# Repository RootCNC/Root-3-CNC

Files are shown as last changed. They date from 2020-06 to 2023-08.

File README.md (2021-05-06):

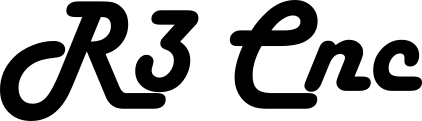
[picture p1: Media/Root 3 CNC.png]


# Root 3 CNC - 3D Printed CNC Machine 

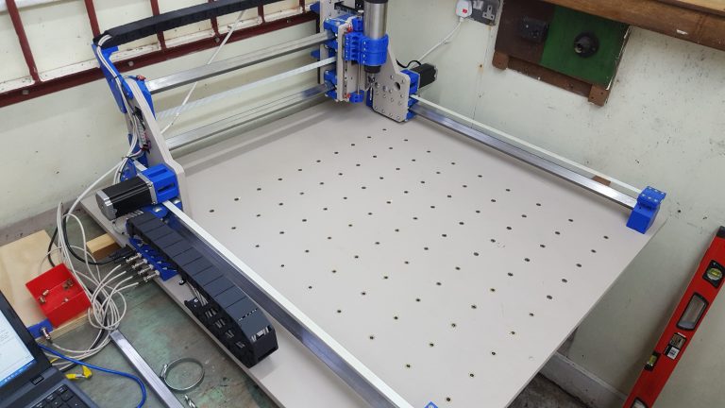
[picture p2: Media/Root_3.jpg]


R3 is the third incarnation of the Root CNC. I have been completely blown away with the community which has been created by this project and listening to all the comments and suggestions made – R3 was created. R3 Is keeping to the same design goals as before, but since then a lot has been learnt and areas for improvements been highlighted. There have been many changes implemented on this revision, some radical and some minor though all the changes have been implemented to increase configurability, rigidity, flexibility, accuracy and also reduce the amount of different parts required.

R3 now supports the largest of NEMA23 motors and also the NEMA17s motors depending on the user’s configuration. Its accuracy has also been increased by the removal of the second loop of belt on the Y-Axis whilst still keeping the two side of the gantry still connected together. The second loop of belt introduced a position error when a load was applied to the gantry, now there is only single belt length to increase its positional accuracy. By doing this made it difficult to keep the two sides of the gantry relatives to one another (something another 3D printed CNCs suffer with). Though R3 gantry sides are connected together, so no matter if the machine losses power or is disconnect the machine still stays relevant to one another to keep its running true and square.

Belt or Lead screw? This has been an interesting topic but no matter what your preference is, R3 has provisions for a Lead screws as drive mechanism for both the X and Y Axis. This does require some of your own design work to fit the type of Lead screw the individual is running though the core R3 shouldn’t need any modification and will work with Belt of Lead screws.

Linear guides for the Z axis?! I know theses aren’t considered cheap. But once all the variables and benefits have been factored in, they become a compelling option to use. especially for the short lengths the Z axis requires. With the original design (R2) there was sufficient play in the carriage, due to its minimalist design. Though R3 has attempted to removed or possibility of play with the wood panel and the use of Linear guides. But don’t think this is the only limited to linear guides, R3 keeps legacy support implementing the same linear bearing style design and also legacy Z carriages.
## Goals

 - Create an expandable CNC machine capable to machine aluminium
 - Use minimal different 3D printed parts 
 - Customization (Make it Bigger)
 - Use different motor and drive methods
 - Cheap   
 - Simple  
 - Use parts commonly used in DIY 3D printer   
 - Easily sourced parts
## BOM (Bill Of Materials)
see [HERE for more information](https://rootcnc.com/machines/root-3/bill-of-materials/)
## Where can I download it from
For the latest and greatest - please use GitHub
Github (Latest files) - [LINK](https://github.com/RootCNC/Root-3-CNC) 
Thingiverse - [LINK](https://www.thingiverse.com/thing:1750276)
## Videos
### Assembly guilds 
(http://www.youtube.com/watch?v=VfKX0M21cGE "")
### Milling Plywood
(http://www.youtube.com/watch?v=CBPlBkgISfY "")
### First Movements
(http://www.youtube.com/watch?v=zV66W9bVTgU "")
### Dry Run
(http://www.youtube.com/watch?v=VkSvLdQc4Qw "")

## License

This project is licensed under the Creative Commons 4.0 license with 
Attribution-NonCommerial-ShareAlike see `LICENSE.txt` for details

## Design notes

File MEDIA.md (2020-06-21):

# Media
Links to non-official videos of the Root 3 cnc. Just a few of the videos that the community has created. Feel free to add more!

## Demonstrations
- [plasma cutter](https://www.youtube.com/watch?v=4bUiL51nPEU)
- [mdf](https://www.youtube.com/watch?v=HNyUsCajYws)
- [laser, in polish](https://www.youtube.com/watch?v=8oZk74TXRVo)
- [laser](https://www.youtube.com/watch?v=Lp46dZl_eGw)
- [mdf, from sailorpete himself](https://www.youtube.com/watch?v=v6d2QQCTKL8)
- [plywood](https://www.youtube.com/watch?v=qoaiHhIS8y8)
- [no cutting, just moving](https://www.youtube.com/watch?v=_PqRj57KkUw)
- [dremel 3000 as spindle](https://www.youtube.com/watch?v=9FLgetXrfY0)
- [plywood, with dust shoe)(https://www.youtube.com/watch?v=5yzxbGJIvBg)

## Build process
- [Timelapse of first half of build, no voiceover](https://www.youtube.com/watch?v=sJdK4KLR89o)
- [second half of build, no voiceover](https://www.youtube.com/watch?v=9sj80fLrxw4)
- [carriages assembly, has a great google doc in the description](https://www.youtube.com/watch?v=mLDNwsXnJGA)
- [box section carriages assembly, has a great google doc in the description)(https://www.youtube.com/watch?v=ErkqIhtdq1w)

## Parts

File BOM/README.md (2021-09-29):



# Root 3 CNC Bill of materials
The Root 3 CNC is configurable in many ways, here are a few configurations you'll need to consider before building one.

Please note an Excel document can be downloaded for more information - [Link](https://github.com/RootCNC/Root-3-CNC/blob/master/BOM/R3%20BOM.xlsx)
#### Belt Options:
 - 2mm GT2 Belts
 - 3mm HTD Belts (Advised option)
#### Box section Options
 - 25x25mm Box section (Metric) 
 - 1"x1" Box section (Imperial)
#### Motor Section
Root 3 CNC can accommodate either NEMA 17 or NEMA 23 Motors. If budget allows, I would recommend the NEMA 23 motor defined in the list below
### Spindle Options
Root 3 supports a number of Spindle sizes:
 - 52mm
 - 65mm
 - 80mm
#### Coach bolts
Coach bolts are optional for the 3D printed carriage if you want a low profile mounting. if you choose to use coach bolts to mount the two carriages together, then you'll need half coach and half standard (this information in the Excel Bill of Materials)
# 3D Printed Parts required
Please note the Root 3 CNC machine can be configured for **different belt sizes** and **different box section sizes**. 
| 3D Printed Parts | Required | QTY | Alternative |
|---|---|---|---|
| Box Section Linear (\*1) | YES | 8 ||
| Y Axis Bar Mount (\*2) (\*3) Mirror | YES | 2 ||
| Y Axis Bar Mount (\*2) (\*3) STD | YES | 2 ||
| X Axis Belt Clamp (\*3) Belt Plate | YES | 2 ||
| X Axis Belt Clamp (\*3) | YES | 2 ||
| Motor Mount (\*4)| YES | 2 ||
| 50mm Spacer (\*4)| YES | 2 ||
| X Carriage Belt Idler | YES | 1 ||
| Y Axis Dust Cover Spacer | NO | 4 ||
| Y Gantry Bearing Cap | YES | 1 |
| Y Gantry Bearing Cap (Cable mount) | YES | 1 ||
| Y Gantry Bearing Space | YES | 2 ||
| Y Gantry Box Mount Foot | YES | 4 |
| Y Gantry Box Section Belt Clamp | YES | 4 ||
| Y Gantry Motion Link | YES | 2 ||
| Z Axis Bearing Cup Bottom | YES | 1 ||
| Z Axis Bearing Cup Top | YES | 1 |Z Axis Bearing Cup Top - Limit Tab Removed<br />Allows clearance for router (Makita in my case) by removing the upper Z limit switch tab |
| MGN 12 Spindle mount (\*5) (Text) | YES | 1 ||
| MGN 12 Spindle mount (\*5)  | YES | 1 ||
| X Axis Drag Chain mount X carriage | YES | 1 ||
| X Axis Drag Chain Mount Y Side panel | YES | 1 ||
| Y Axis Drag Chain mount to  X carriage | YES | 1 ||
| Drag Chain Y Carriage Mount | YES | 1 ||

(\*1) Optional Configuration: for standard M8 Bolts print x8 Guild STD and for Coach bolt print x8 Guild STD and 4x COACH BOLT
(\*2) Select box section size
(\*3) Select Belt type 
(\*4) Select Motr size 
(\*5) Select Spindle size 

# Panels
| Item | QTY | Link|
|---|---|-----|
| Side_Panel|2|[Root CNC Store](https://rootcnc.com/product/root-3-side-panel/)|
| Z_Axis_WoodPanel_Front|1|[Root CNC Store](https://rootcnc.com/product/root-3-front-rear-x-carriage-z-plate/)|
| Z_Axis_WoodPanel_Rear|1|[Root CNC Store](https://rootcnc.com/product/root-3-front-rear-x-carriage-z-plate/)|

Wooden Panel kits can be found [HERE](https://rootcnc.com/product/root-3-cnc-starter-pack/) 

# Electronics/ Electro Mechanical
| Item | Required | QTY | Link|
|---|---|---|-----|
| 23HS41-1804S NEMA 23 1.8deg 2.4Nm (340oz.in) 1.8A | YES | 4 | [LINK](https://www.omc-stepperonline.com/nema-23-bipolar-1-8deg-2-4nm-340oz-in-1-8a-4-95v-57x57x104mm-4-wires.html/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)|
| NEMA 17 Bipolar 1.8deg 65Ncm (92oz.in) 2.1A |NO |4| [LINK](https://www.omc-stepperonline.com/nema-17-bipolar-1-8deg-65ncm-92oz-in-2-1a-3-36v-42x42x60mm-4-wires-it.html/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)|
| 1.5KW Spindle with VFD|YES|1|[LINK_1](https://s.click.aliexpress.com/e/_dX0JKm3) [LINK_2](https://s.click.aliexpress.com/e/_dT4xs63) [LINK_3](https://s.click.aliexpress.com/e/_dSjt6gr) [LINK_4](https://s.click.aliexpress.com/e/_dSUhh43)
| 400W Quiet Spindle (not recommended)|NO |||
| Micro Switch SPDT micro switch V4 KW11i|YES|6|[LINK UK](https://amzn.to/31Kf1wC) [LINK](https://s.click.aliexpress.com/e/_ATnQCz)| 
| 12V or 24V PSU (For Controller power + any lights) |YES|1|[12V_LINK_UK](https://amzn.to/2HxYvIS) [12V_lINK](https://s.click.aliexpress.com/e/_AACYyd)| 
| Aviation plug (GX12) |NO|x|[LINK_UK](https://amzn.to/31LBPfl) [LINK](https://s.click.aliexpress.com/e/_AtqbWz)|
| Stepper Motor Drivers (E.G DRV8825)| YES | 4||
| Cooling Fan - 60mm DC Fan | YES | 1 ||
| 4 Core AWG24/26 Cable | YES |||
| Arduino Mega With RAMP kit ||||
| Root CNC GRBL controller comming soon ||||

# Motion
| Item | Required | QTY | Link|
|---|---|---|-----|
|608 Bearings | Yes | 56 |[LINK_UK](https://amzn.to/3dWB9c6) [LINK](https://s.click.aliexpress.com/e/_ATuujF)|
|MGN12 200mm + (MGN12C x2) | Yes | 2 |[LINK]()|
|R38 18mm x 37mm Black Drag Chain 1M | Yes | CNC Size dependant |[LINK_UK](https://amzn.to/37J6PAH)  [LINK](https://s.click.aliexpress.com/e/_9hJS33)|
|3M HTD Belt | Yes | CNC Size dependant (2x Y Axis Length + 1x X Axis Length = min belt length) |[LINK_UK]()  [LINK]()|
|HTD 3M Round Tooth Timing Belt Pulley 8mm Bore 24T*| Yes | 5/7 |[LINK]()|
|HTD 3M Round Tooth Timing Belt Pulley 8mm Bor 20T*| Yes | 2 |[LINK]() |
|HTD 3M Round Tooth Timing Belt 9mm Wide 345-3M-9| Yes | 1 |[LINK_UK]() [LINK]()

(\*) Dependant on stepper motor selection - This configuration will work for the above stepper motor from OMC Stepper Motor Online

# Hardware
Below is guide on the QTY required/ the pack sizes I brought to assemble the Root 3 CNC
| Item | Required | QTY | Link|
|---|---|---|-----|
|Box section 25x25xX/Yx3mm (W,D,L,T)(\*)|YES|4||
|M3 Penny Washers (Large)|YES|100|YES||
|M3 Machine Screws (16,20,25,30,40 mm)|YES|100|YES||
|M3 Nuts|YES|100|YES||
|M3 Rivit Nuts|YES|16|YES||
|M4 Penny Washers (Large)|YES|30|YES||
|M4 x40mm Bolt|YES|20|YES||
|M4 x 35mm Countersunk Screw|YES|32|YES||
|M4 Nuts|YES|50|YES||
|M5 x70mm Bolt with Washer head|YES|8|YES||
|M5 Washers|YES|8|YES||
|M5 Nuts|YES|8|YES||
|M8 Axis Connecting Bar|YES|1|YES||
|M8 Lead screw / Threaded Rod|YES|1|YES||
|M8 x25mm Herx Head Bolt|YES|32|YES||
|M8 x75mm Bolt|YES|20|YES||
|M8 x75mm Coach Bolt|NO|20|NO||
|M8 Washers|YES|100|YES||
|M8 Nuts|YES|100|YES||
|M8 Collar|YES|4|YES||
|M8 Tee Nuts|NO||NO||

(\*) Length of the box section is dependant on size of the machine you are building - use this link for more information [LINK](https://rootcnc.com/machines/root-3/root-3-dimensions/)

# MISC Items
| Item | Required | QTY | Link|
|---|---|---|-----|
|Mist Coolant Lubrication Spray System Unit (Used for Airline to Spindle - Aluminium machining)| No |1 | |

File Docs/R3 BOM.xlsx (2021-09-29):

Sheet: 3D Printed Parts
Item | QTY | Printed | Config | Stepper Config | 1" or 25mm Box | Belt Size | Notes
Box Section Linear Guild STD | 8 | No | Default | N/A | N/A | N/A
* Optional Config |  |  |  |  |  |  | Results in a tidyer looking machine but does require M8 Coach bolts with filled edges
-- Box Section Linear Guild STD | 4 | No | Optional | N/A | N/A | N/A
-- Box Section Linear Guild COACH BOLT | 4 | No | Optional | N/A | N/A | N/A
1" Square Box section |  |  |  |  |  |  | Use this subsection over 25mm box section if you plan to use 1" box section
-- X Axis Box Section Mount 1'x1' | 2 | No | Default | N/A | 1" | N/A
* 2mm Pitch belt
-- Y Axis Bar Mount 1'x1' 2mm Mirror | 2 | No | Default | N/A | 1" | GT2 (2mm)
-- Y Axis Bar Mount 1'x1' 2mm STD | 2 | No | Default | N/A | 1" | GT2 (2mm)
-- X Axis Belt Clamp 2mm GT2 Belt Plate | 2 | No | Default | N/A | 1" | GT2 (2mm)
-- X Axis Belt Clamp 2mm GT2 | 2 | No | Default | N/A | 1" | GT2 (2mm)
* 3mm Pitch Belt
-- Y Axis Bar Mount 1'x1' 3mm Mirror | 2 | No | Default | N/A | 1" | 3M HTD (3mm)
-- Y Axis Bar Mount 1'x1' 3mm STD | 2 | No | Default | N/A | 1" | 3M HTD (3mm)
-- X Axis Belt Clamp 2mm 3M HTD Belt Plate | 2 | No | Default | N/A | 1" | 3M HTD (3mm)
-- X Axis Belt Clamp 2mm 3M HTD | 2 | No | Default | N/A | 1" | 3M HTD (3mm)
25mm Square Box section |  |  |  |  |  |  | Use this subsection over 1" box section if you plan to use 25mm box section
-- X Axis Box Section Mount 25x25 | 2 | No | Default | N/A | 25mm | N/A
* 2mm Pitch belt
-- Y Axis Bar Mount 25x25 2mm Mirror | 2 | No | Default | N/A | 25mm | GT2 (2mm)
-- Y Axis Bar Mount 25x25 2mm STD | 2 | No | Default | N/A | 25mm | GT2 (2mm)
-- X Axis Belt Clamp 2mm GT2 Belt Plate | 2 | No | Default | N/A | 25mm | GT2 (2mm)
-- X Axis Belt Clamp 2mm GT2 | 2 | No | Default | N/A | 25mm | GT2 (2mm)
* 3mm Pitch Belt
-- Y Axis Bar Mount 25x25 3mm Mirror | 2 | No | Default | N/A | 25mm | 3M HTD (3mm)
-- Y Axis Bar Mount 25x25 3mm STD | 2 | No | Default | N/A | 25mm | 3M HTD (3mm)
-- X Axis Belt Clamp 2mm 3M HTD Belt Plate | 2 | No | Default | N/A | 25mm | 3M HTD (3mm)
-- X Axis Belt Clamp 2mm 3M HTD | 2 | No | Default | N/A | 25mm | 3M HTD (3mm)
Motor Mount NEMA17 | 2 | No | Optional | NEMA17 | N/A | N/A
NEMA17 50mm Spacer | 2 | No | Optional | NEMA17 | N/A | N/A
Motor Mount NEMA23 | 2 | No | Default | NEMA23 | N/A | N/A
NEMA23 50mm Spacer | 2 | No | Default | NEMA23 | N/A | N/A
X Carriage Belt Idler | 1 | No | Default | N/A | N/A | N/A
Y Axis Dust Cover Spacer | 4 | No | Optional | N/A | N/A | N/A | Spacer when fitting dust cover to the Y axis
Y Gantry Bearing Cap | 1 | No | Default | N/A | N/A | N/A
Y Gantry Bearing Cap (Cable mount) | 1 | No | Default | N/A | N/A | N/A
* Optional Config |  |  |  |  |  |  | If cable management is required
-- Y Gantry Bearing Cap | 1 | No | Optional | N/A | N/A | N/A
-- Y Gantry Bearing Cap W/ cable clip | 1 | No | Optional | N/A | N/A | N/A
Y Gantry Bearing Space | 2 | No | Default | N/A | N/A | N/A
Y Gantry Box Mount Foot | 4 | No | Default | N/A | N/A | N/A
Y Gantry Box Section Belt Clamp | 4 | No | Default | N/A | N/A | N/A
Y Gantry Motion Link | 2 | No | Default | N/A | N/A | N/A
Z Carriage - Linear Guild (Recomened)
Z Axis Bearing Cup Bottom | 1 | No | Default | N/A | N/A | N/A
Z Axis Bearing Cup Top | 1 | No | Default | N/A | N/A | N/A
Z Axis Bearing Cup Top - Limit Tab Removed | 1 | No | Optional | N/A | N/A | N/A | Allows clearance for router (Makita in my case) by removing the upper Z limit switch tab
Spindle Options
MGN 12 Spindle mount 52mm (Text) | 1 | No | Optional | N/A | N/A | N/A
MGN 12 Spindle mount 52mm (NO Text) | 1 | No | Optional | N/A | N/A | N/A
MGN 12 Spindle mount 65mm (Text) | 1 | No | Default | N/A | N/A | N/A | I currently us a VFD spindle
MGN 12 Spindle mount 65mm (NO Text) | 1 | No | Default | N/A | N/A | N/A | I currently us a VFD spindle
MGN 12 Spindle mount 80mm (Text) | 1 | No | Optional | N/A | N/A | N/A
MGN 12 Spindle mount 80mm (NO Text) | 1 | No | Optional | N/A | N/A | N/A
X Axis Drag Chain mount X carriage | 1 | No | Default | N/A | N/A | N/A
X Axis Drag Chain Mount Y Side panel | 1 | No | Default | N/A | N/A | N/A
Y Axis Drag Chain mount to X carriage | 1 | No | Default | N/A | N/A | N/A
Drag Chain Y Carriage Mount | 1 | No | Default | N/A | N/A | N/A

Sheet: Nut and Bolt
Item | QTY | Config | Stepper Config | 1" or 25mm Box | Belt Size | Notes
M3 Penny Washers (Large) | Lots
M3 Machine Screws (Different lengths) | Lots |  |  |  |  | x16,20,25,30,40 mm Lengths (good to have a selection on hand)
M3 Nuts | Lots
M3 Rivit Nuts | 16 |  |  |  |  | (FN02991) used to mount the MGN rail to the wooden board
M4 Penny Washers (Large) | Lots | Default | N/A | N/A | N/A
M4 x40mm Bolt | 20
M4 x 35mm Countersunk Screw | 32
M4 Nuts | Lots
M5 x70mm Bolt with Washer head | 8 |  | NEMA23 |  |  | Used on the Y axis side pannel to mount the Nema 23s
M5 Washers | 8
M5 Nuts | 8 |  |  |  |  | Used on the Y axis side pannel to mount the Nema 23s
M8 Axis Connecting Bar | 1 |  |  |  |  | Length is size dependant on machine
M8 Lead screw / Threaded Rod | 1 |  |  |  |  | 400mm cut to length
M8 x25mm Herx Head Bolt | 32
M8 x75mm Bolt | 20 | Default
M8 x75mm Coach Bolt | 20 | Optional
M8 Washers | Lots
M8 Nuts | Lots
M8 Collar | 4
M8 Tee Nuts |  | Optional |  |  |  | Used to mount work pieces to the bed
MGN12 200mm | 2
MGN12C | 4
3M HTD Belt | 1 |  |  |  |  | Length is size dependant on machine
24T 3M HTD 8mm Pulley | 5/7 |  |  |  |  | Used on the X/Y Axis Motion note the bore of your stepper motors!
20T 3M HTD 8mm Pulley | 2 |  |  |  |  | Used for the Z Axis
345-3M-9 | 1 |  | NEMA23 |  |  | Used to link the Z axis
608 Bearing | 56
Drag Chain 18x37mm Open | 2
Aluminum Box section 25x25xX/Yx3mm (W,D,L,T) | 4 | Default | N/A
Steel Box section 25x25xX/Yx2mm (W,D,L,T) | 4 | Optional | N/A

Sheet: Electronics
Item | QTY | Ordered? | Notes
PSU | 1 | No
-12V 100W+ (Stepper motors Only) |  | No | Currently use a over kill 400W PSU for Stepper motors only
- Spindle PSU (Dependant on Spindle choose!) |  | No | Will be required with DC motors Like the orginal used in R2
Stepper Motor Drivers | 4 | No
- DRV8825 |  | No | Currently used on R2 & R2.1
- A4988 |  | No | I would recomd the DRV8825 driver instead of theses
- More to come… |  | No
Stepper Motors | 4 | No
- NEMA 17 |  | No
--- 42BYGHW609 4000g/cm 1.7A |  | No | Used on R2 Y,Z axis
--- 17HS24-2104S |  | No | Used on R2 X axis
- NEMA 23 |  | No
---23HS41-1804S |  | No | Currently used on all axis on R2.1
Motion Controller | 1 | No
- Arduino Mega (Ramps 1.4 - Marlin Firmware) |  | No | Currently used on all my machines
- Arduino Uno (GRBL with CNC sheild) |  | No | Not used
Endstops | 6 | No
- KW11 Micro switches |  | No | Used on all my machines
- LJ12A3-4-Z/BY Inductive Sensor |  | No | My ideal option but more costly
Controller/ Stepper motor driver Cooling Fan | 1 | No
- 60mm DC Fan |  | No | Or other Size but needed to keep the drivers running cool
Cabling |  | No
- 4 Core AWG24/26 Cable |  | No | Used for Stepper motors and Endstop
~~- Ethernet Cable~~ |  | No | Not recommened due to high chance of breakage due to movement (Google "Work Hardening" - due to the single cores/strand used it Cat cabling)
Spindle | 1 | No
- Quiet Cut Spindle (300W 48V DC motor) |  | No | Used on R2 Requires an aditional PSU as stated un PSU section
- 400W 48V DC motor |  | No | Requires an aditional PSU as stated un PSU section
- VDF Spindle |  | No | Currently using a 1.5kW aircooled VFD spindle on R2.1 well worht it ( 1.5KW Air-cooled Spindle motor/ .5kw Variable Frequency Drive inverter)

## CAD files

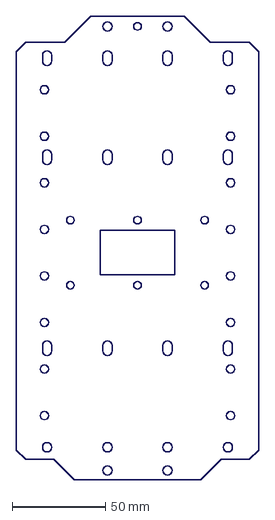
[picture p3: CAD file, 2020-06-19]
DXF_Files/X Carriage Rework wood pannel FRONT.DXF
130.0 x 249.0 mm

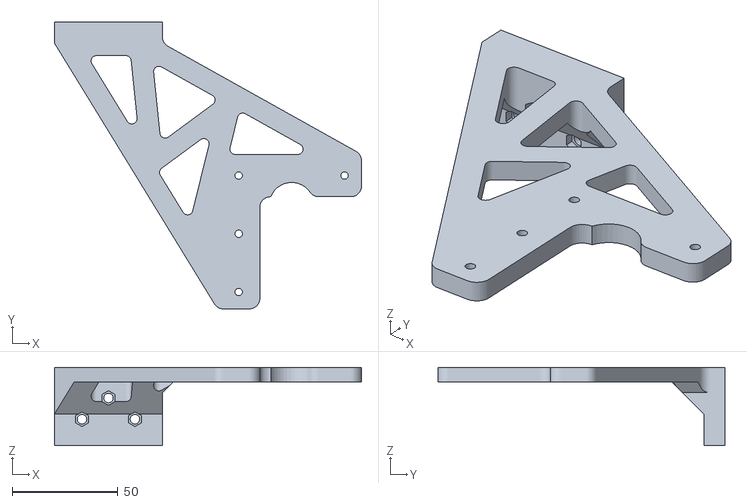
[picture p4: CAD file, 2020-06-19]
STL_Files/Drag Chain Mounts/X Axis/X Axis Drag Chain Mount Y Side panel.STL
145.0 x 135.5 x 37.0

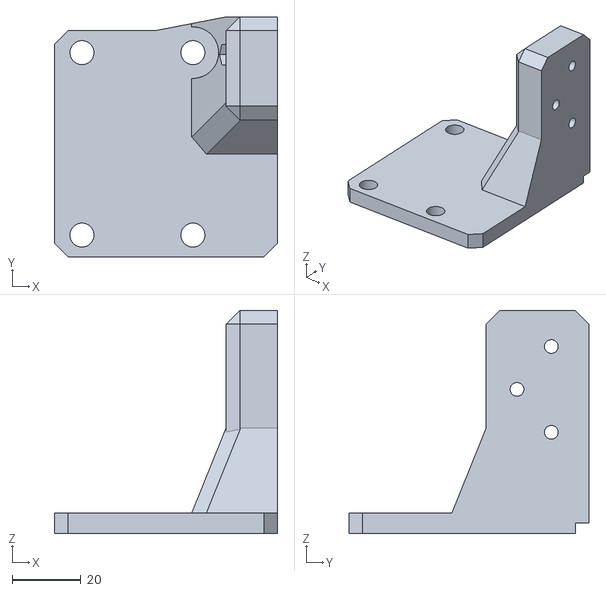
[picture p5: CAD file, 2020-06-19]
STL_Files/Drag Chain Mounts/Y-Axis/Drag Chain Y Carriage Mount.STL
65.0 x 70.0 x 65.0

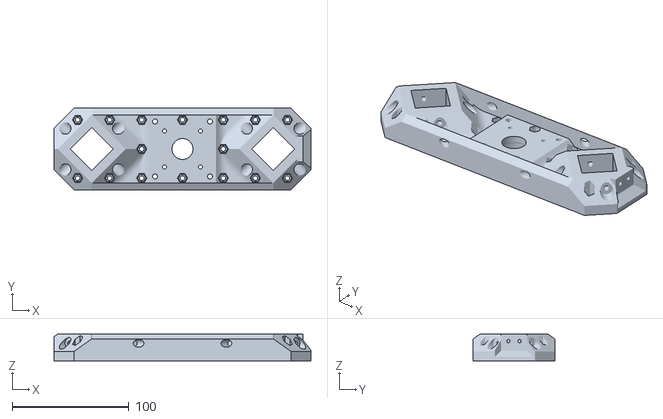
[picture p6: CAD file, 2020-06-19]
STL_Files/X Carriage/1'x1'/X Axis Box Section Mount 1'x1'.STL
220.6 x 70.0 x 23.0

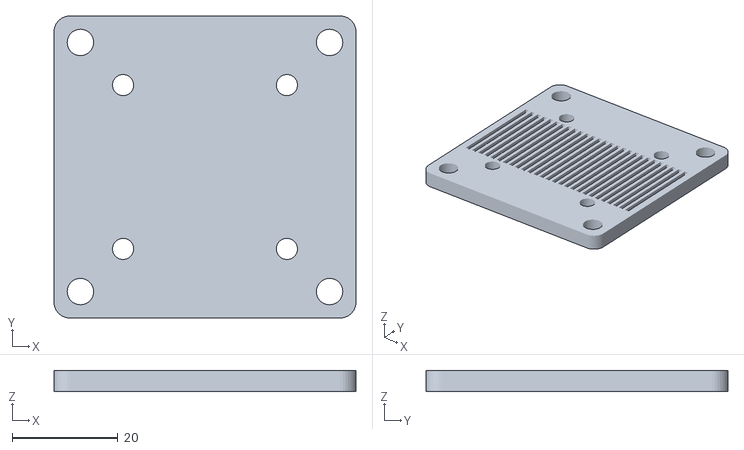
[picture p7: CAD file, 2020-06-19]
STL_Files/X Carriage/X Axis Belt Clamp 2mm GT2 Belt Plate.STL
57.1 x 57.1 x 4.00

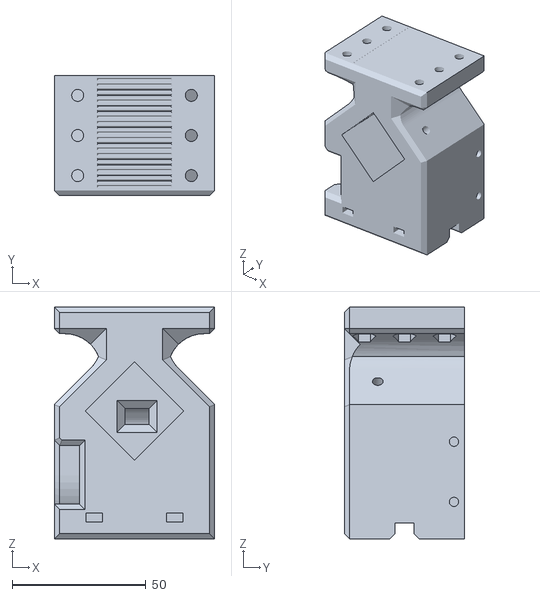
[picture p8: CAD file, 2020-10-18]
STL_Files/Y Carrage/1'x1'/2mm Pitch Belt/Y Axis Bar Mount 1'x1' 2mm STD IssB.STL
60.0 x 45.0 x 86.8

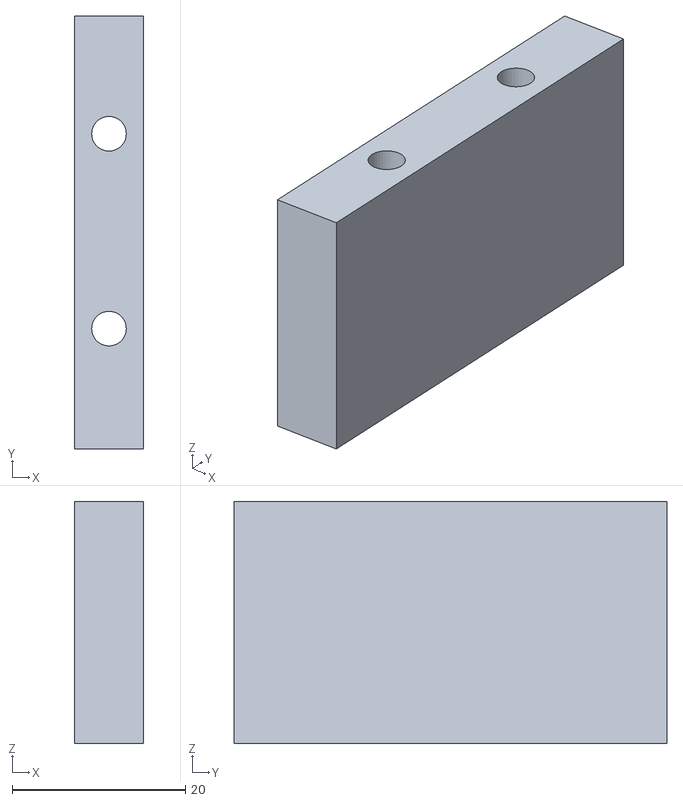
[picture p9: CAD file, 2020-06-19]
STL_Files/Y Carrage/Y Axis Dust Cover Spacer.STL
8.00 x 50.0 x 28.0

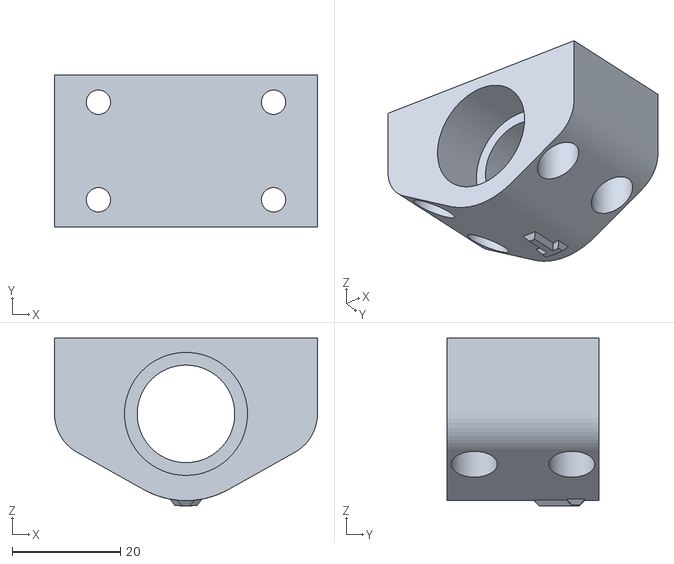
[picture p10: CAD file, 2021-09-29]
STL_Files/Z Axis/Linear Guild (Recomenned)/Z Axis Bearing Cup Top - Limit Tab Removed.stl
48.5 x 28.0 x 31.0

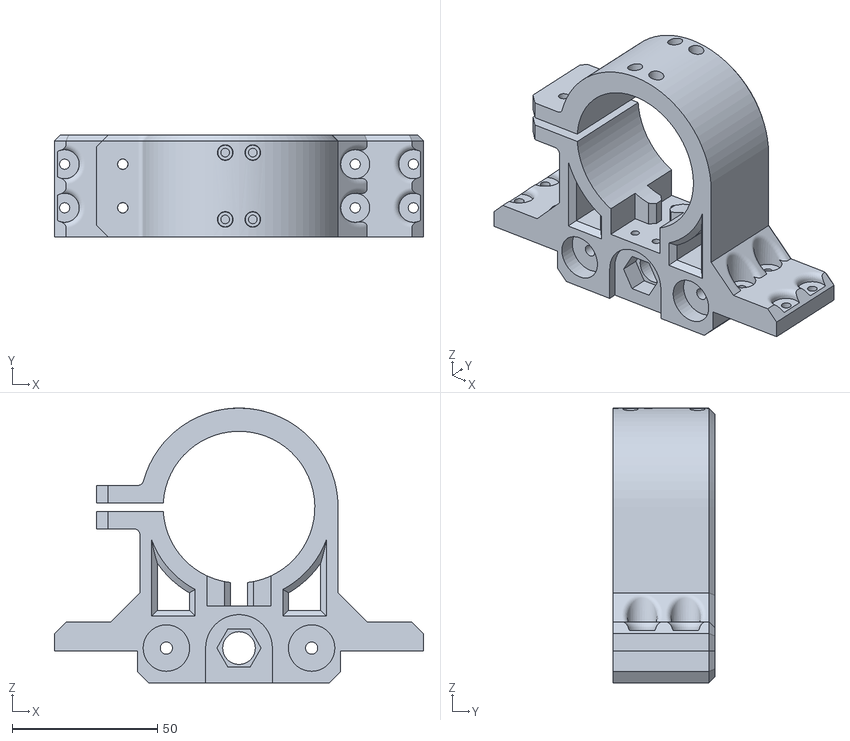
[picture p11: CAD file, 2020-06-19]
STL_Files/Z Axis/Linear Guild (Recomenned)/Z Carriages/52mm/MGN 12 Spindle mount 52mm (NO Text).STL
127.0 x 35.0 x 94.6

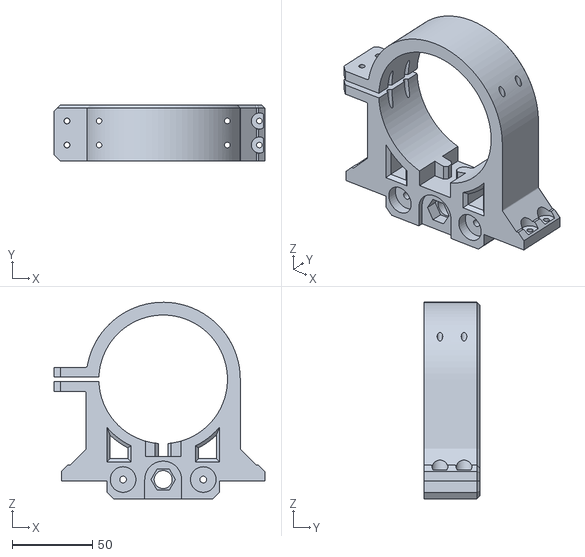
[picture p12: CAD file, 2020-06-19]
STL_Files/Z Axis/Linear Guild (Recomenned)/Z Carriages/80mm/MGN 12 Spindle mount 80mm (NO Text).STL
131.6 x 35.0 x 122.6

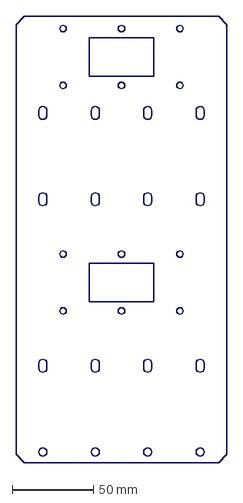
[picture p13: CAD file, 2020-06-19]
DXF_Files/X Carriage Rework wood pannel BACK.DXF
130.0 x 275.0 mm

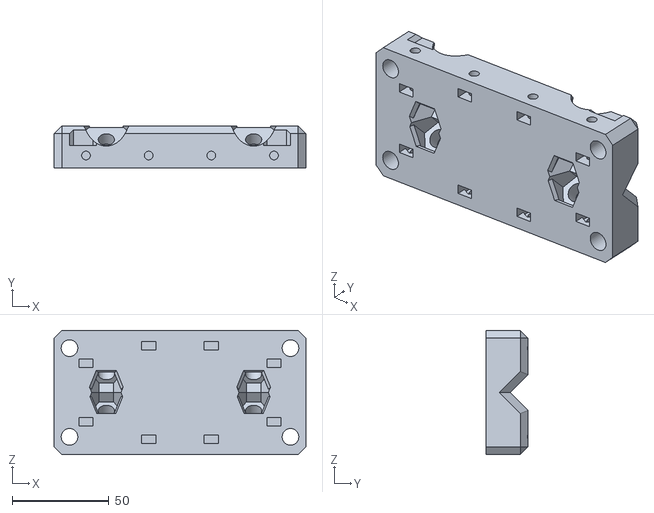
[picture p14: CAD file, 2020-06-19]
STL_Files/Box Section Linear Guild STD.STL
130.0 x 21.8 x 64.0

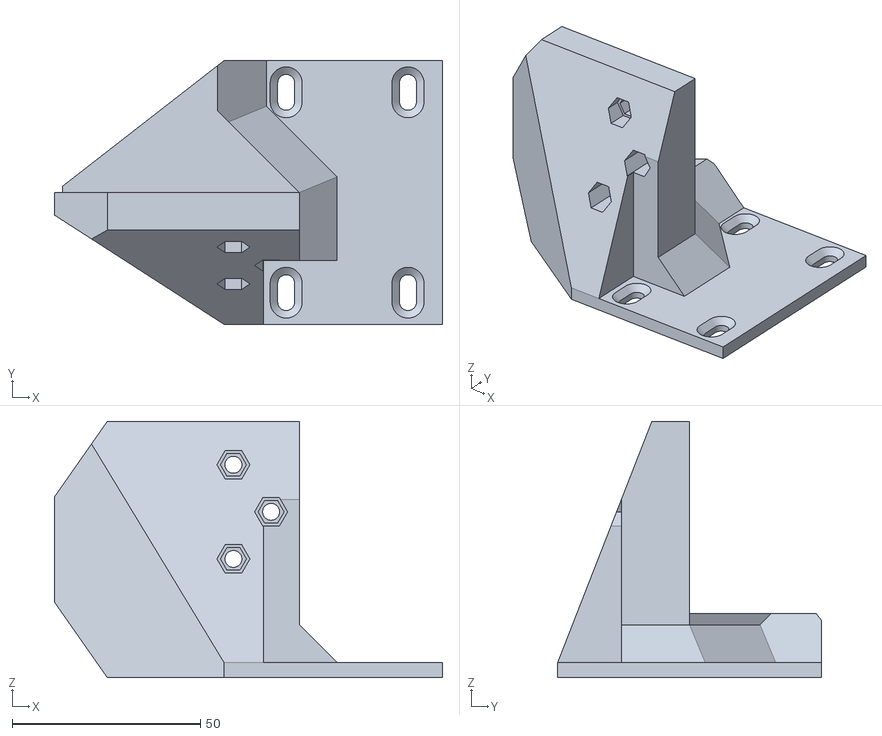
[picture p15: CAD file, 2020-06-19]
STL_Files/Drag Chain Mounts/X Axis/X Axis Drag Chain mount X carriage.STL
103.0 x 70.0 x 68.0

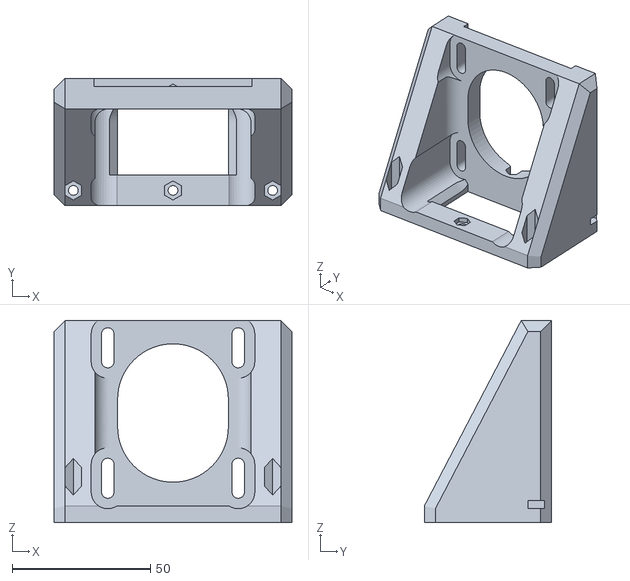
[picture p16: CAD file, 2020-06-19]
STL_Files/X Carriage/Motor Mount NEMA23.STL
86.0 x 46.0 x 73.0

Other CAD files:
STL_Files/X Carriage/25x25mm/X Axis Box Section Mount 25x25mm.STL
STL_Files/Y Carrage/1'x1'/3mm Pitch Belt/Y Axis Bar Mount 1'x1' 3mm STD IssB.STL
STL_Files/Y Carrage/25x25mm/2mm Pitch Belt/Y Axis Bar Mount 25x25 2mm STD IssB.STL
STL_Files/Y Carrage/25x25mm/3mm Pitch Belt/Y Axis Bar Mount 25x25 3mm Mirror IssB.STL
DXF_Files/X Carriage Rework wood pannel UNIVERSAL.DXF
DXF_Files/X side pannel.DXF
STL_Files/Box Section Linear Guild COACH BOLT.STL
STL_Files/Connector Panel.STL
STL_Files/Probe Mount.STL
STL_Files/X Carriage/Motor Mount NEMA17.STL
STL_Files/X Carriage/X Axis Belt Clamp 3M HTD Belt Plate.STL
STL_Files/X Carriage/X Carriage Belt Idler.STL
STL_Files/X Carriage/X axis Belt Mount 2mm.STL
STL_Files/X Carriage/X axis Belt Mount 3mm.STL
STL_Files/Y Carrage/1'x1'/2mm Pitch Belt/Y Axis Bar Mount 1'x1' 2mm Mirror IssB.STL
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

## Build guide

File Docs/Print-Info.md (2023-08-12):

---
title: Root 3 Print Orientation
description: How to print the parts for the Root 3
published: true
date: 2022-06-28T22:24:57.245Z
tags: root 3, how to print
editor: markdown
dateCreated: 2022-06-28T22:17:17.168Z
---

# Box Section Linear Guild STD
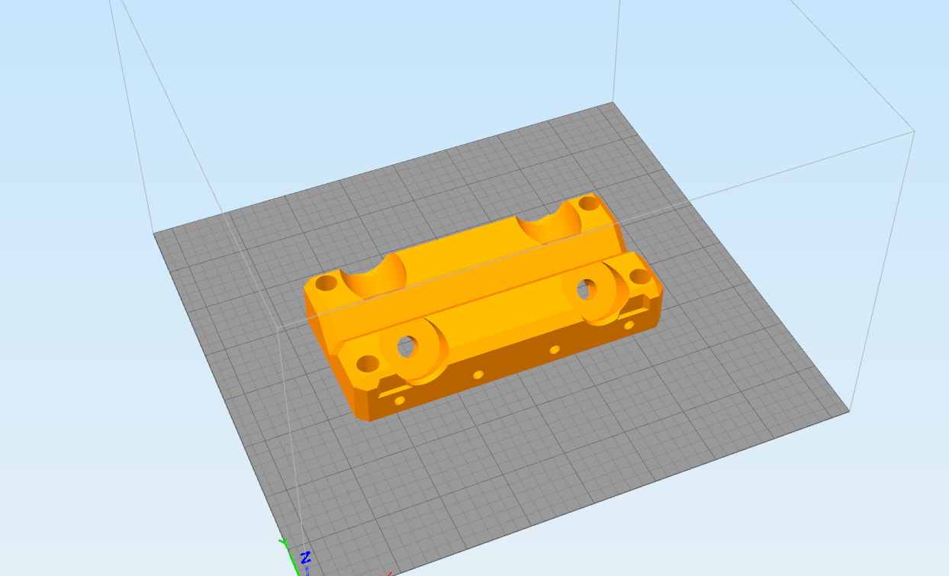
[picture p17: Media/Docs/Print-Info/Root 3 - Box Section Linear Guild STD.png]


# Connector Panel
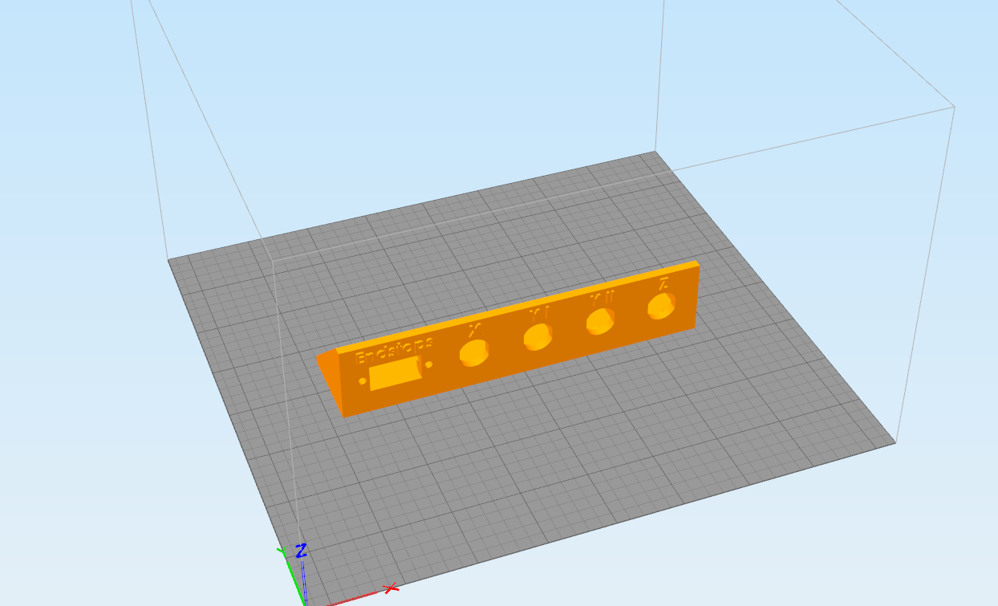
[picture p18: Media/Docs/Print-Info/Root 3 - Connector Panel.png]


# Drag Chain Y Carriage Mount
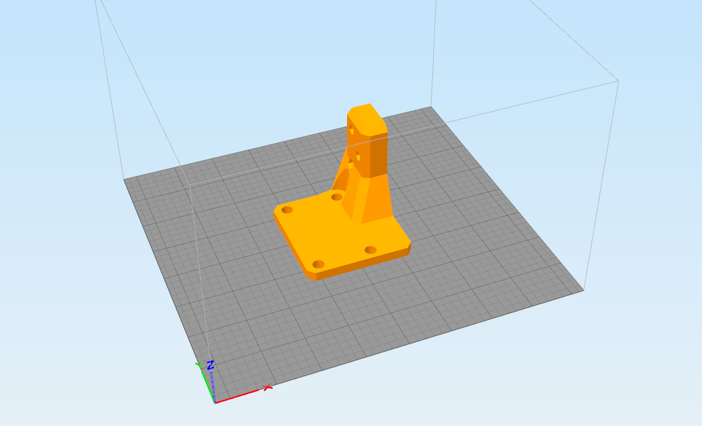
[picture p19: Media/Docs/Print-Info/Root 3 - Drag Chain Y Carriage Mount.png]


# MGN 12 Spindle mount ##mm (Text)- (NO Text)
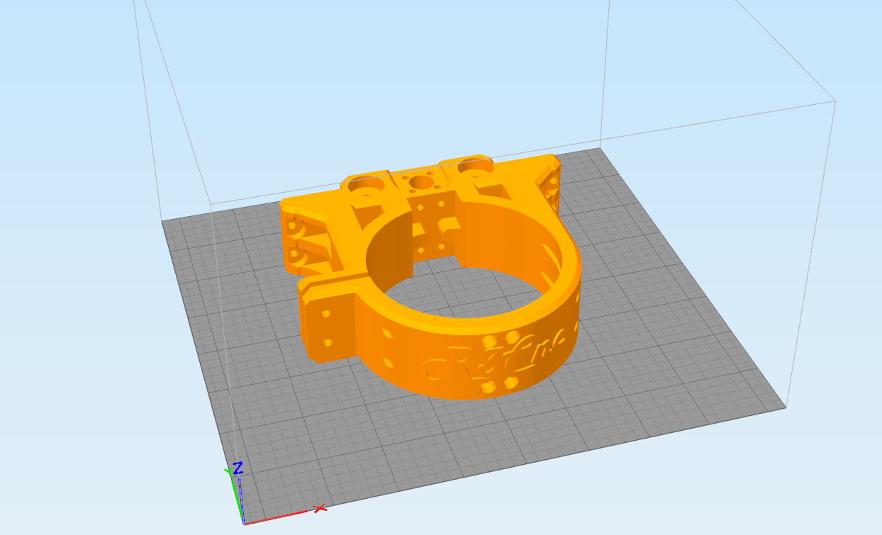
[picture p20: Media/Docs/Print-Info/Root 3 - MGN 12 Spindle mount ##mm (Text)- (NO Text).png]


# Motor Mount NEMA17
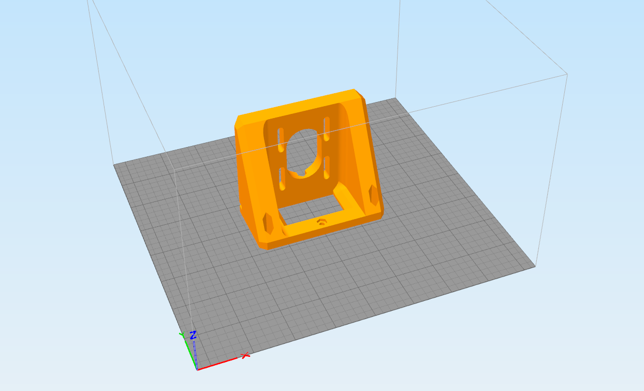
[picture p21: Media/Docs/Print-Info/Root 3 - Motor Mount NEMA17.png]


# Motor Mount NEMA23
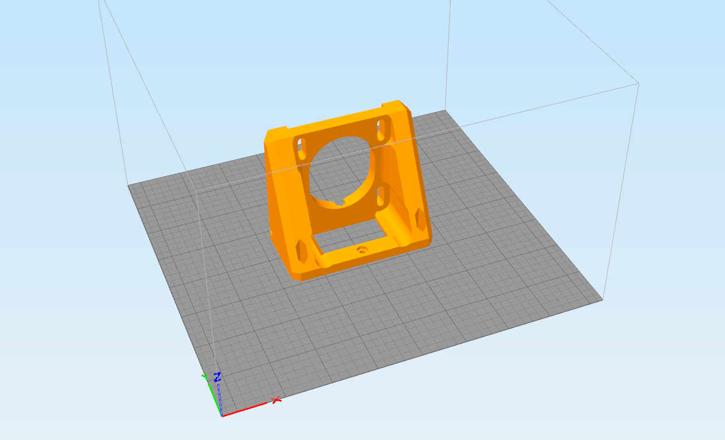
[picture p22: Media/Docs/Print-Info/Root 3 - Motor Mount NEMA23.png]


# NEMA17 50mm Spacer
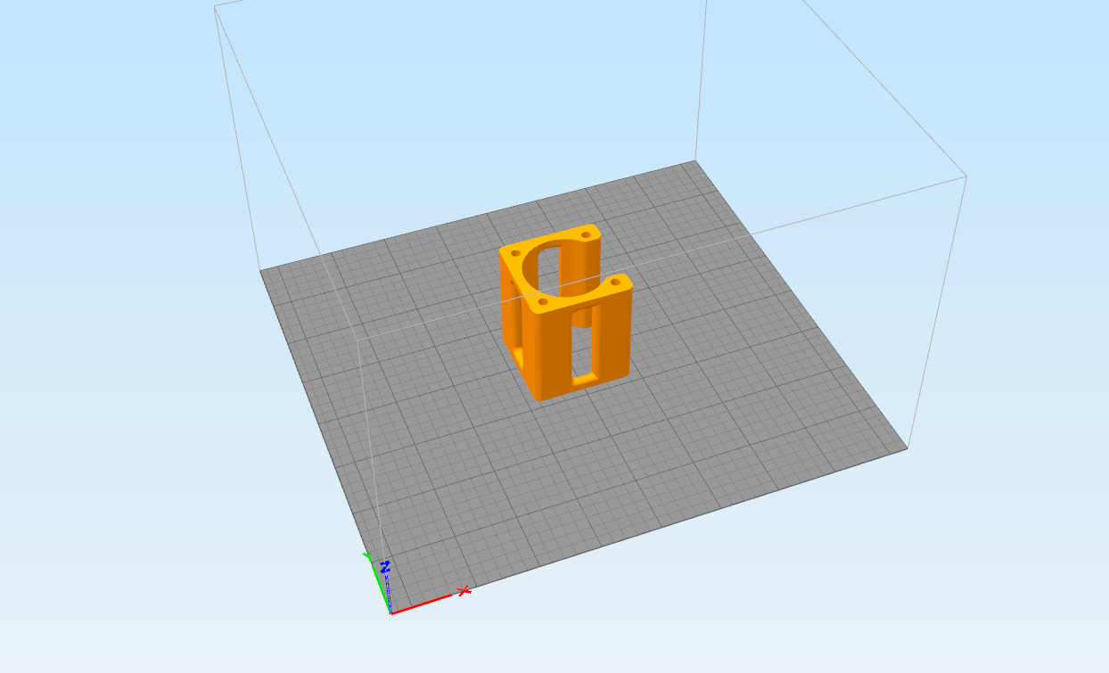
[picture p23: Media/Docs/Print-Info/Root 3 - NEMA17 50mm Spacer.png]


# NEMA23 50mm Spacer
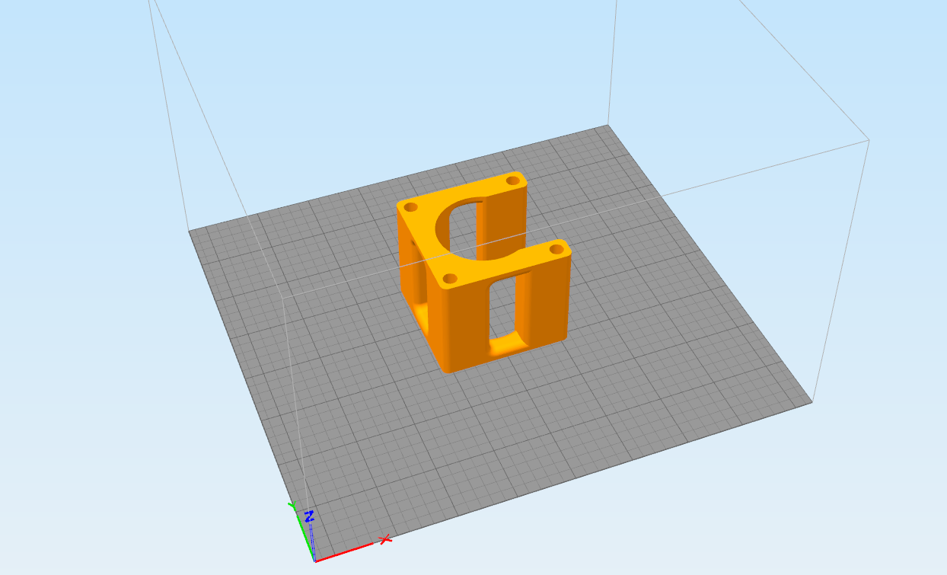
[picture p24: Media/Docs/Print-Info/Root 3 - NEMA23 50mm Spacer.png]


# X Axis Belt Clamp 2mm GT2 Belt Plate
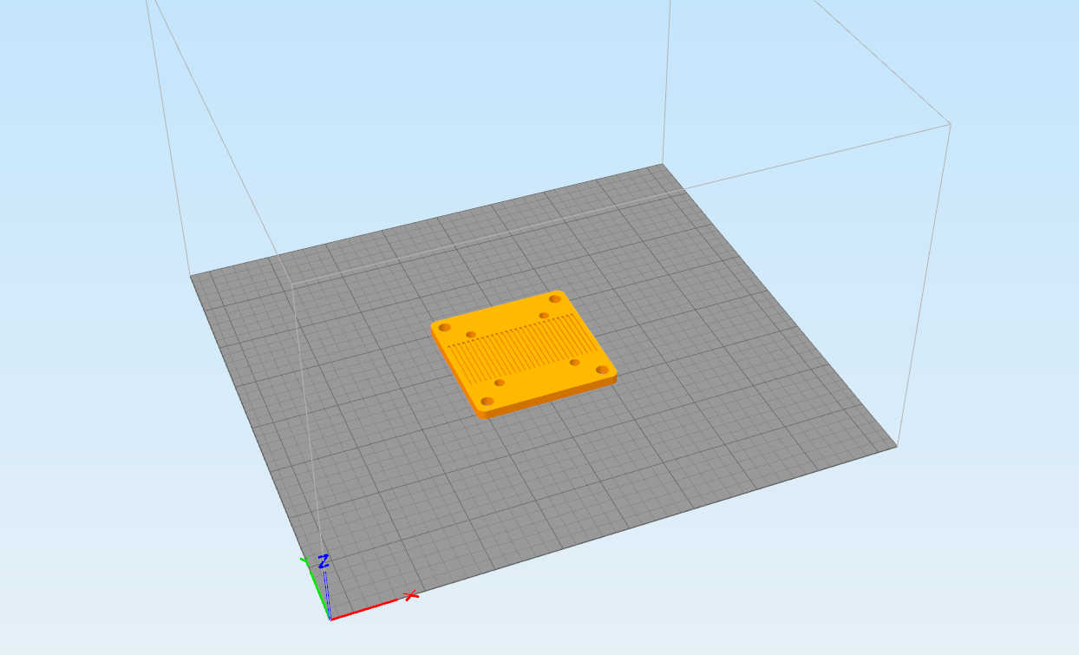
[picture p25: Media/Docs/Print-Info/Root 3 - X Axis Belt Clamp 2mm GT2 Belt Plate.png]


# X Axis Belt Clamp 3M HTD Belt Plate
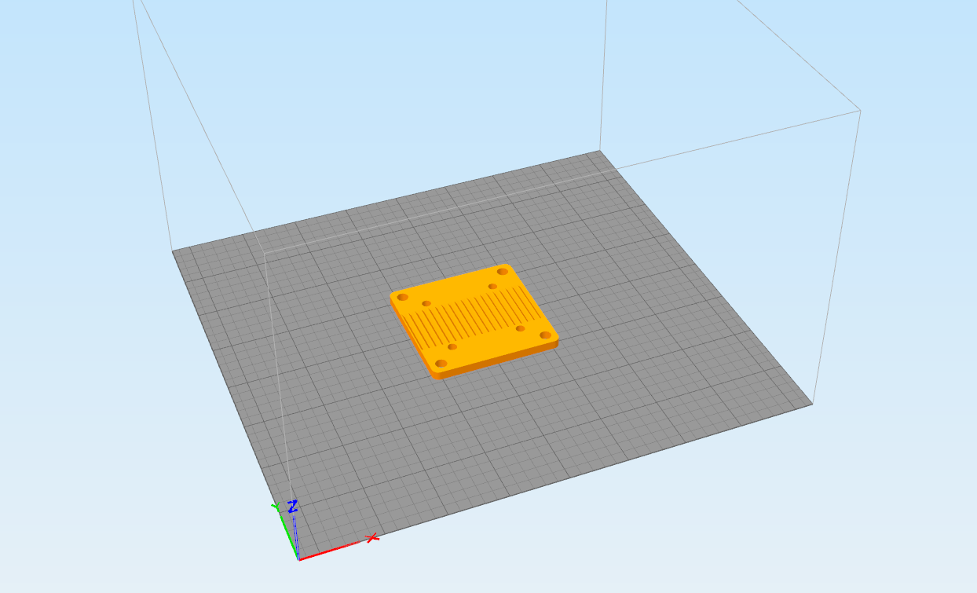
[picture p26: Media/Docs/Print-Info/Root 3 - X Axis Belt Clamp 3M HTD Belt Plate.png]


# X axis Belt Mount #mm
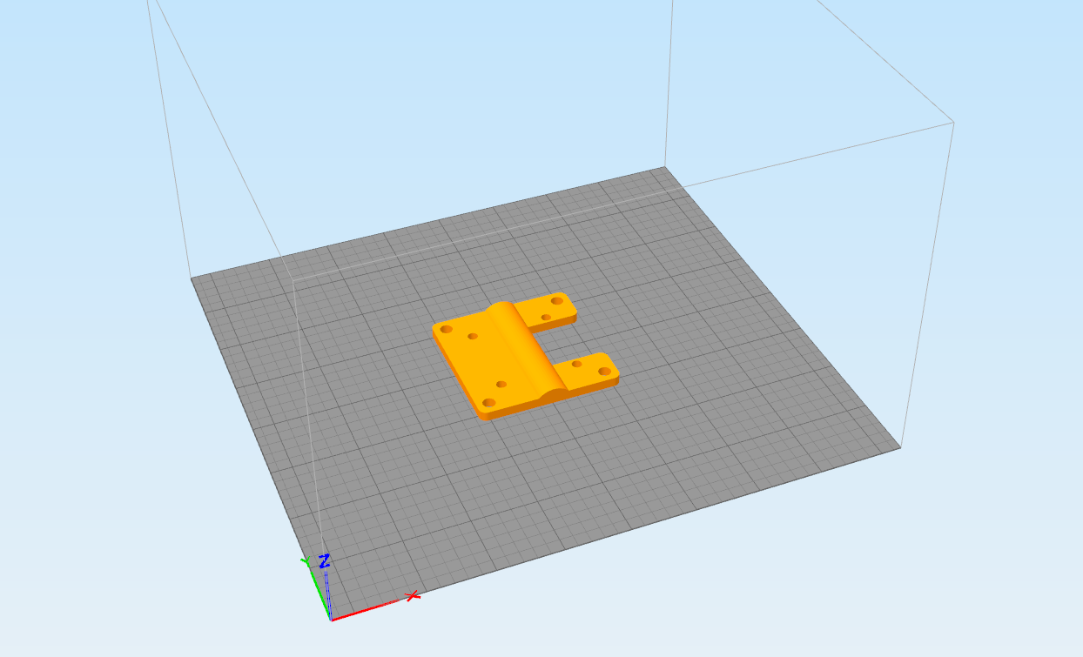
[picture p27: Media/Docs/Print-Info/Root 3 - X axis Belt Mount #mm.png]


# X Axis Box Section Mount ##
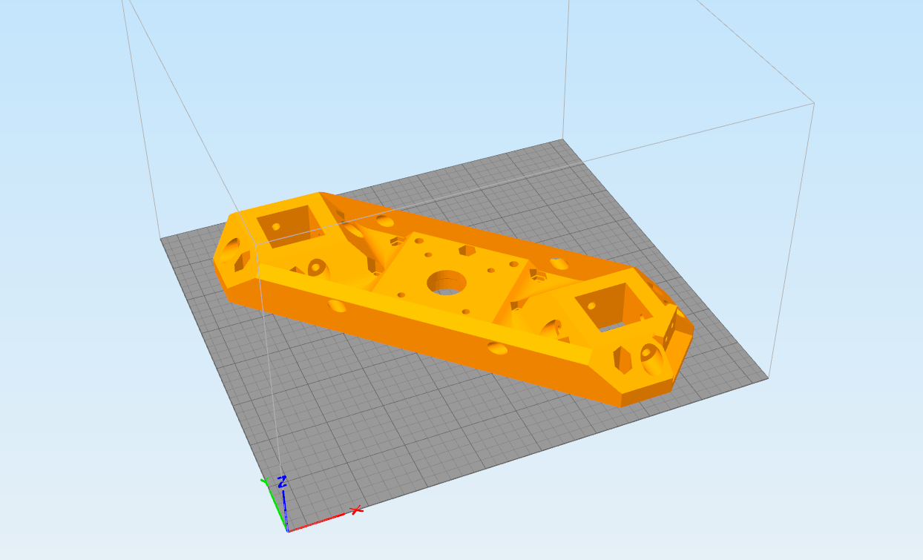
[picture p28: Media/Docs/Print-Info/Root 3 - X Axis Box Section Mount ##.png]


# X Axis Drag Chain mount X carriage
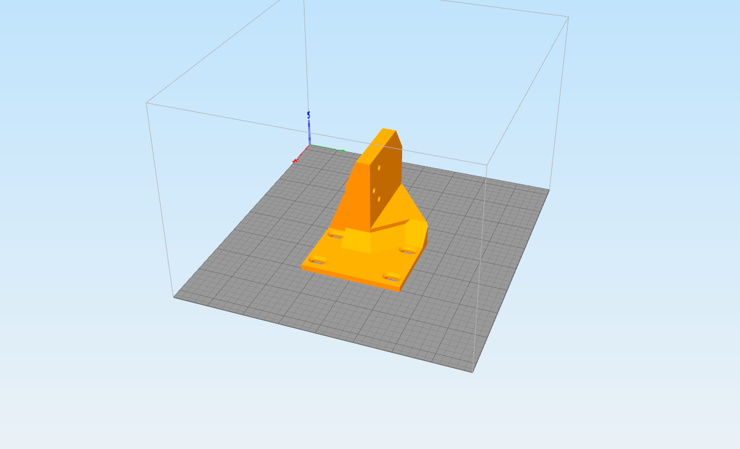
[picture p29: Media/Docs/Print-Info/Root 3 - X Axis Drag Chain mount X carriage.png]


# X Axis Drag Chain Mount Y Side panel
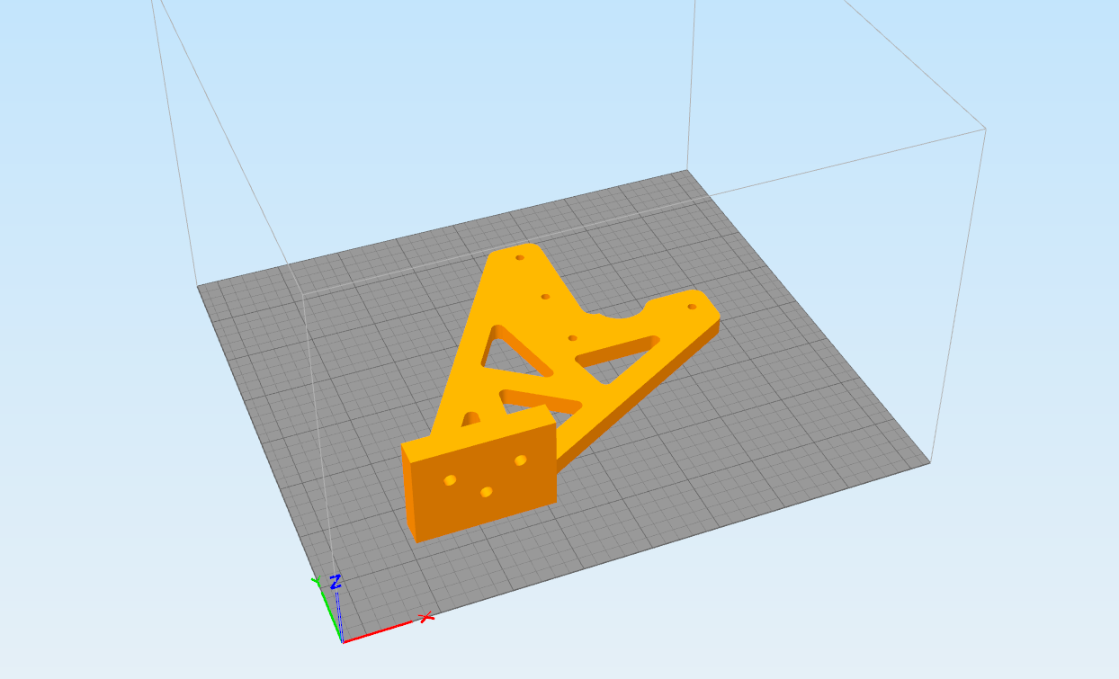
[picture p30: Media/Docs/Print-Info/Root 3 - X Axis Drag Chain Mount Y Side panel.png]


# X Carriage Belt Idler
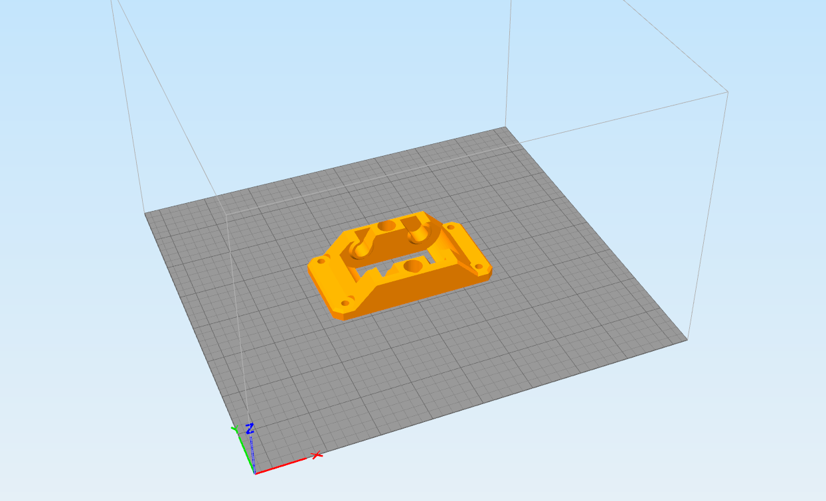
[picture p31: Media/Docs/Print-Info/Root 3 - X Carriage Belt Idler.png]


# Y Axis Bar Mount #x# #mm STD-Mirror
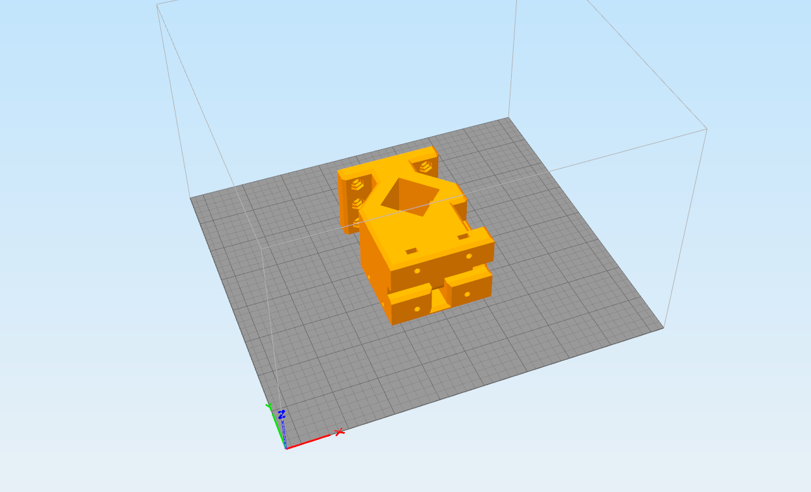
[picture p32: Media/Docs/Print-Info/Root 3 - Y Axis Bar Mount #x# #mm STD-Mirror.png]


# Y Gantry Bearing Cap (Cable mount)
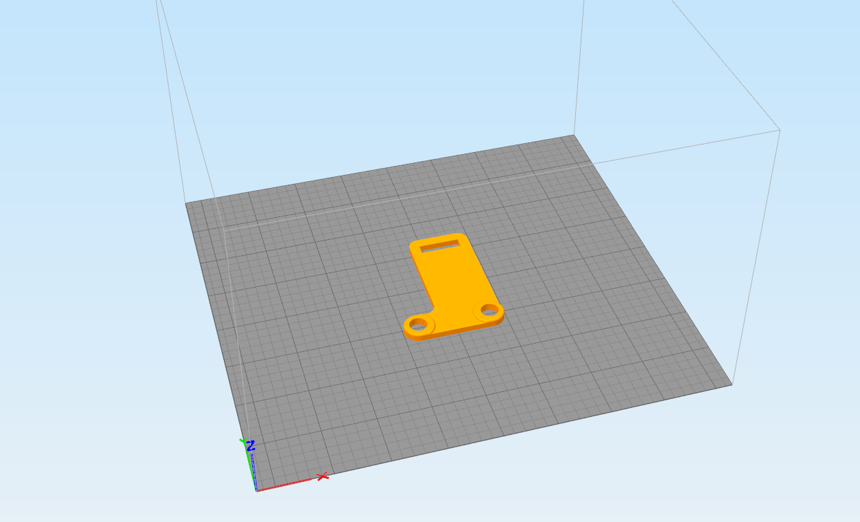
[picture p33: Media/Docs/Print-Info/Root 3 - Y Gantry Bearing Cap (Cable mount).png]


# Y Gantry Bearing Cap
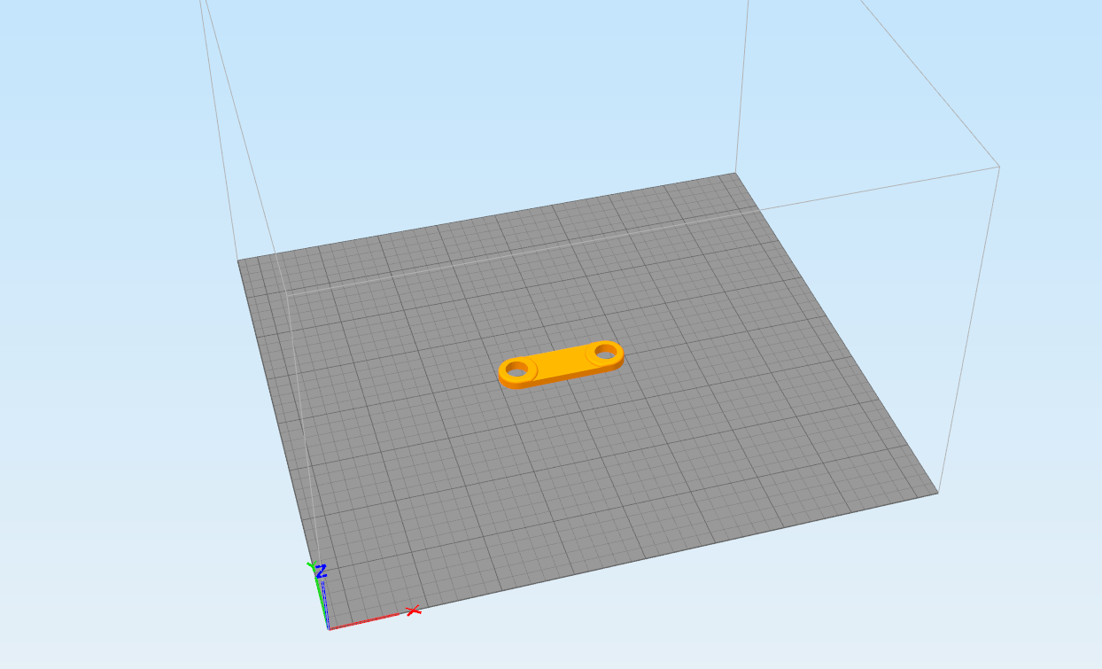
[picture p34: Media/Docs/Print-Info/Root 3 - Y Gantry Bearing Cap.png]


# Y Gantry Bearing Space
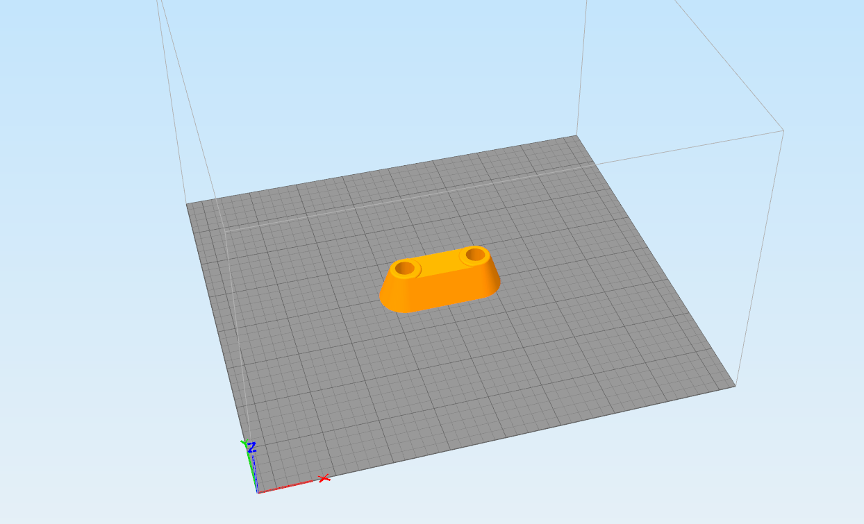
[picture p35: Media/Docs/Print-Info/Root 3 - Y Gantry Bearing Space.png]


# Y Gantry Box Mount Foot
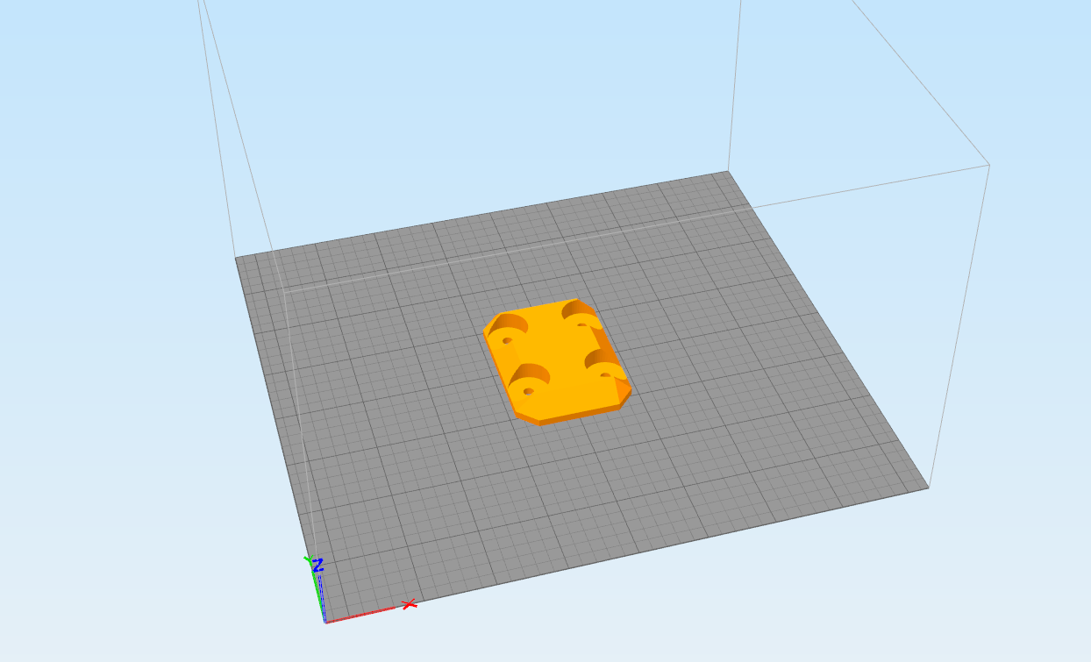
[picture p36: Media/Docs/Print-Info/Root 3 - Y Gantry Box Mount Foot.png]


# Y Gantry Box Section Belt Clamp
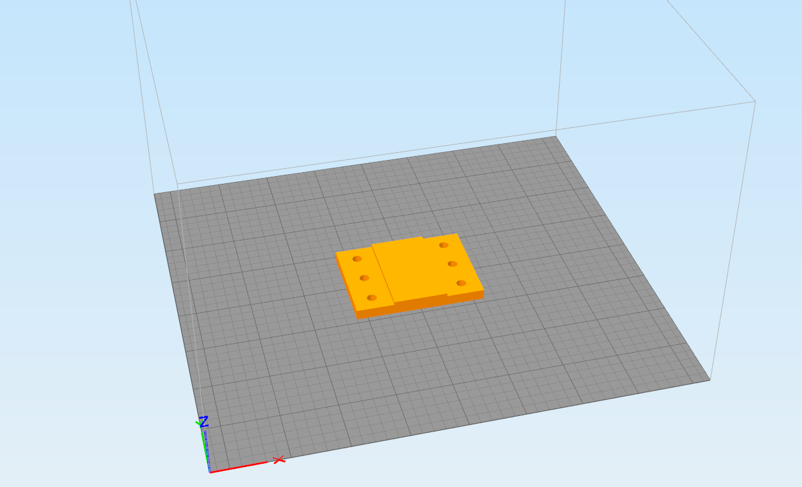
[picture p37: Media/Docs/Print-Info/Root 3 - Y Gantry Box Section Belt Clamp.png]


# Y Gantry Motion Link
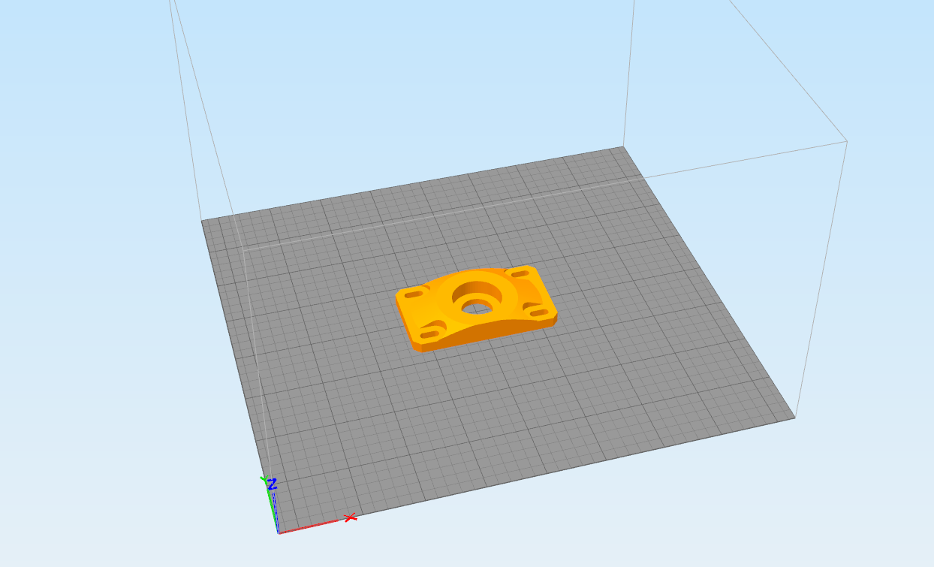
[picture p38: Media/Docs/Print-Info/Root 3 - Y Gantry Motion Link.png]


# Z Axis Bearing Cup Bottom
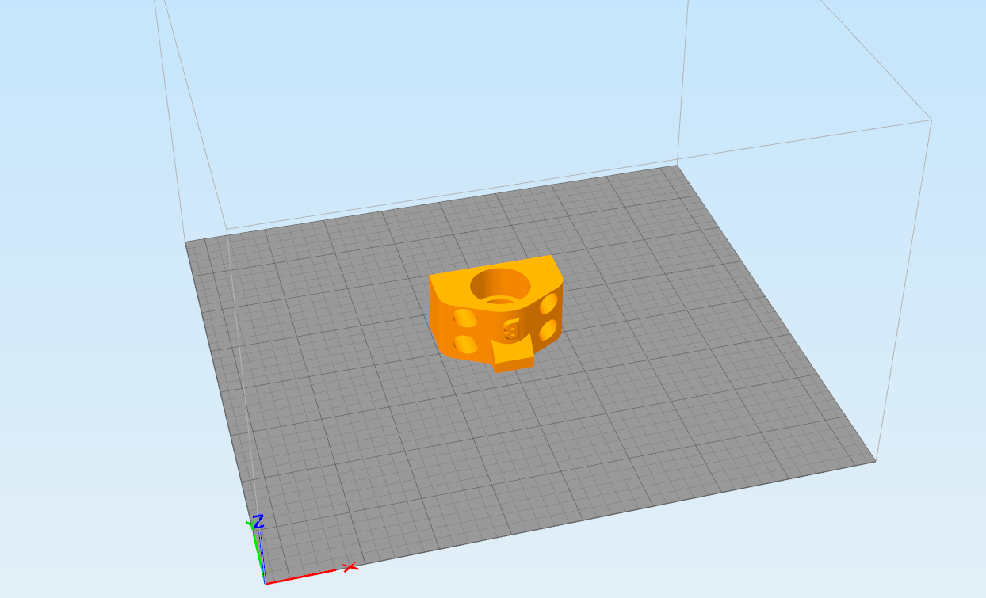
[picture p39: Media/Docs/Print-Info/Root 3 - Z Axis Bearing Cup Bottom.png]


# Z Axis Bearing Cup Top
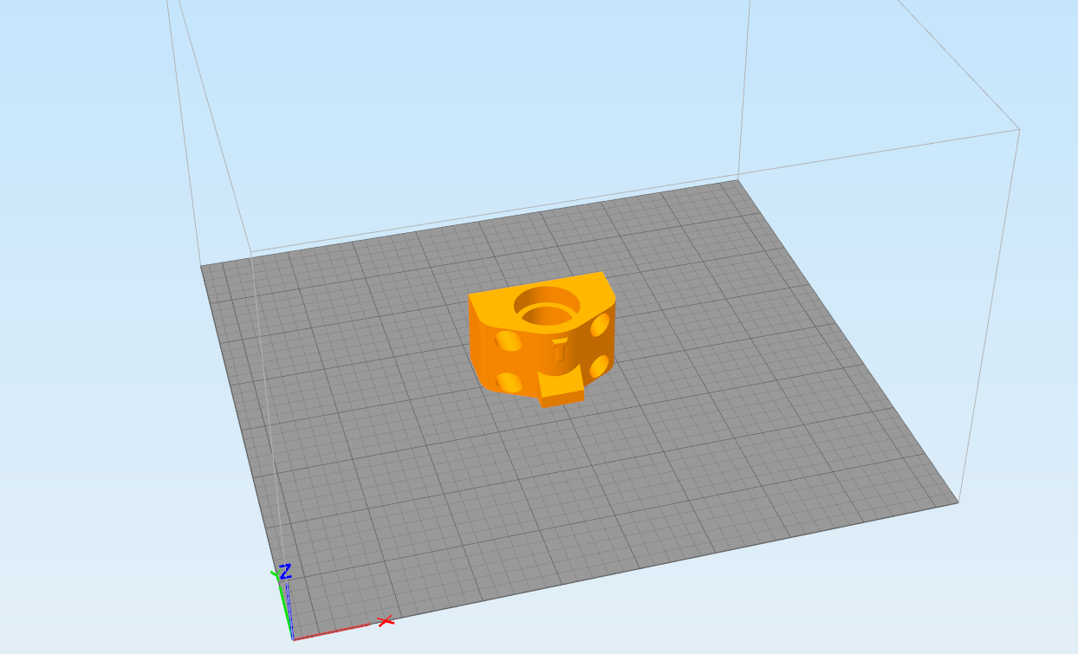
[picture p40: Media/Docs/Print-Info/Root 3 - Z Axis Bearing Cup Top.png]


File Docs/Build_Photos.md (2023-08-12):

---
title: Root 3 Build Photos
description: Build Photos for the Root 3
published: true
date: 2022-06-28T22:24:57.245Z
tags: root 3, how to print
editor: markdown
dateCreated: 2022-06-28T22:17:17.168Z
---

# Build Photos
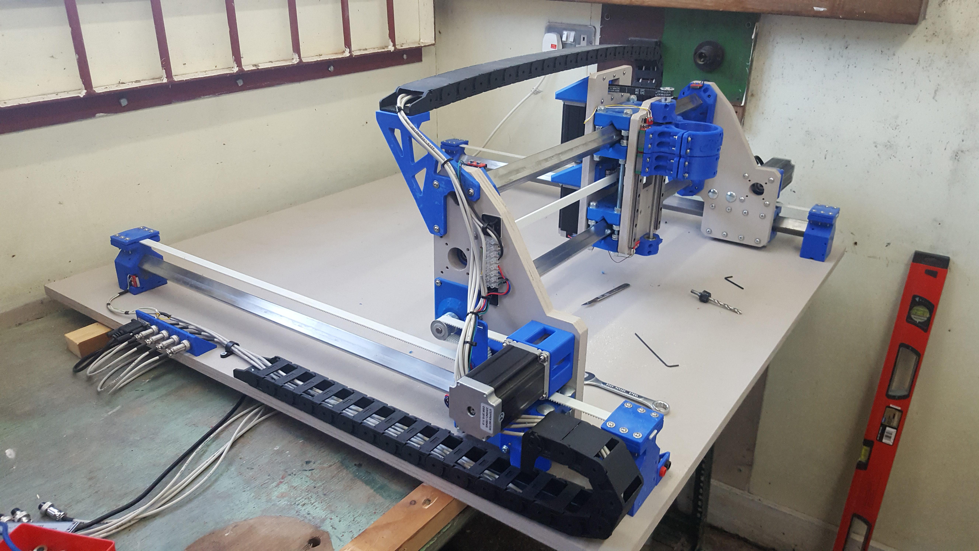
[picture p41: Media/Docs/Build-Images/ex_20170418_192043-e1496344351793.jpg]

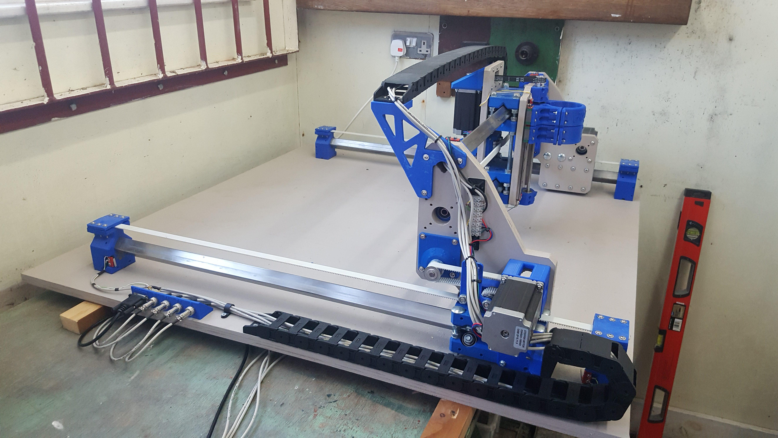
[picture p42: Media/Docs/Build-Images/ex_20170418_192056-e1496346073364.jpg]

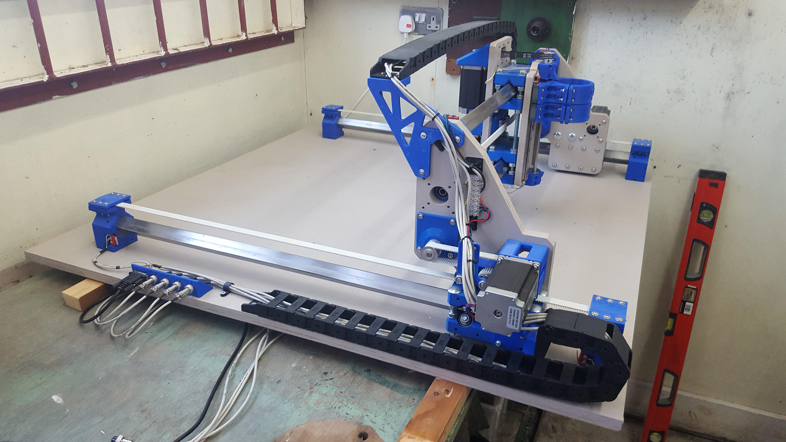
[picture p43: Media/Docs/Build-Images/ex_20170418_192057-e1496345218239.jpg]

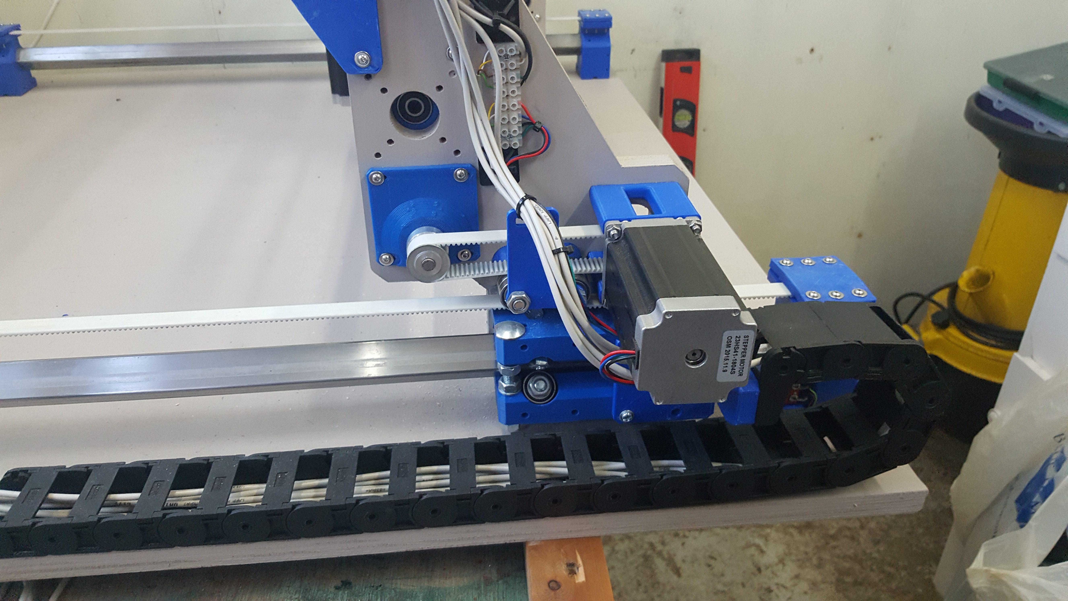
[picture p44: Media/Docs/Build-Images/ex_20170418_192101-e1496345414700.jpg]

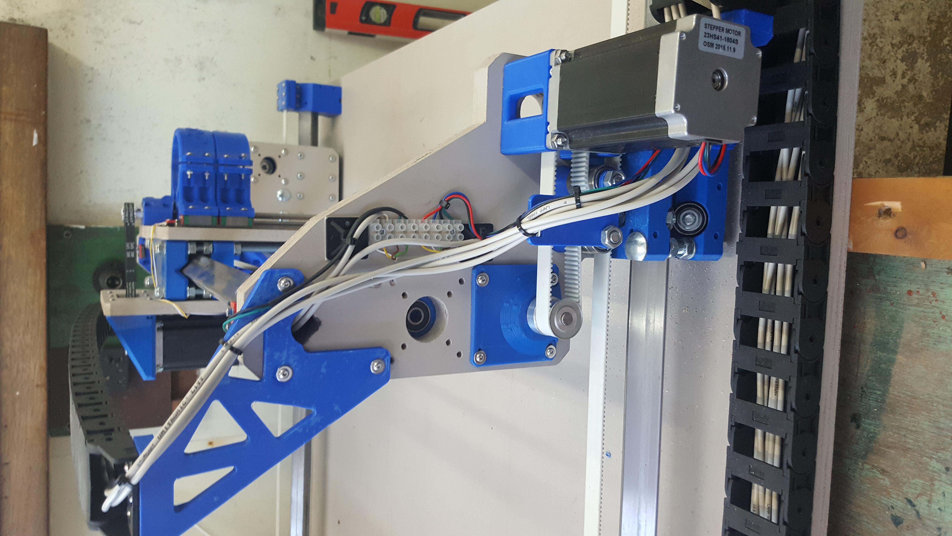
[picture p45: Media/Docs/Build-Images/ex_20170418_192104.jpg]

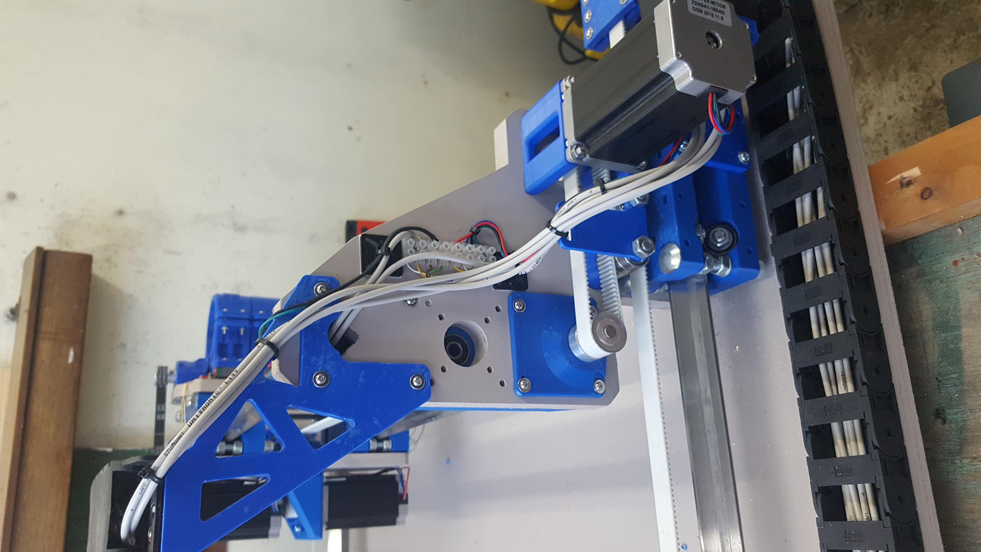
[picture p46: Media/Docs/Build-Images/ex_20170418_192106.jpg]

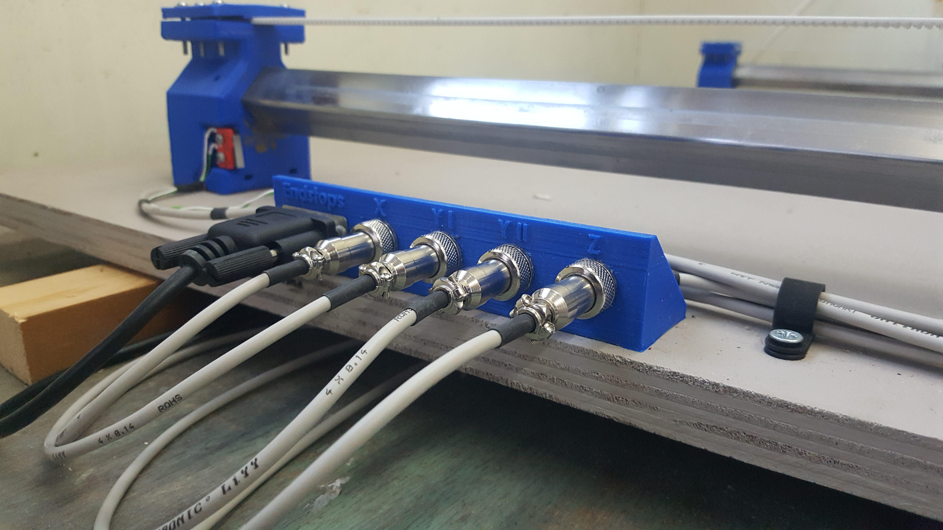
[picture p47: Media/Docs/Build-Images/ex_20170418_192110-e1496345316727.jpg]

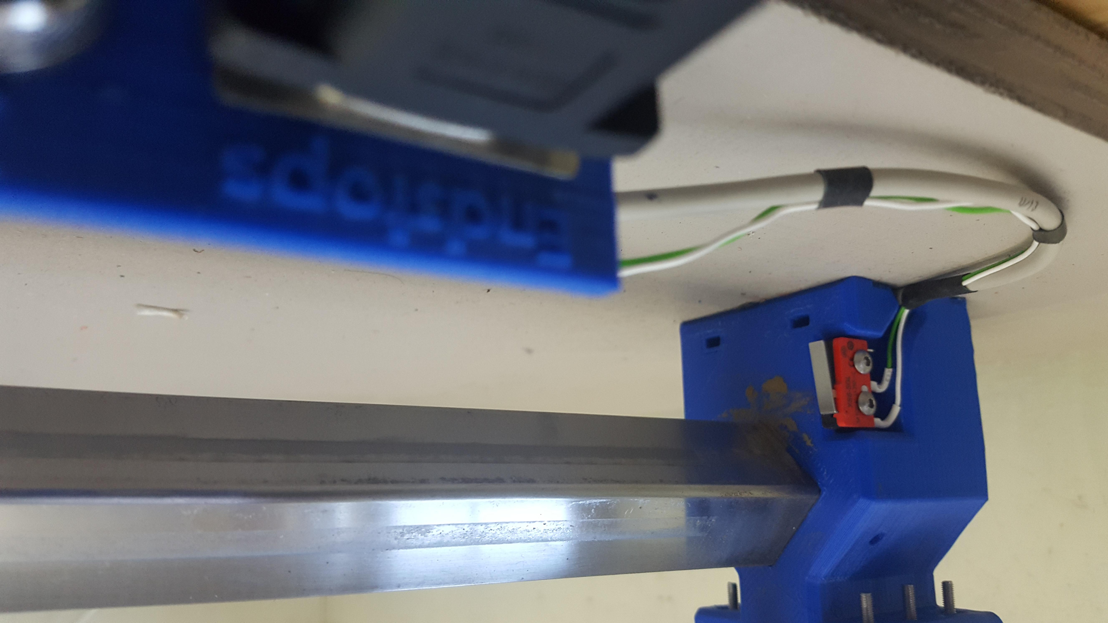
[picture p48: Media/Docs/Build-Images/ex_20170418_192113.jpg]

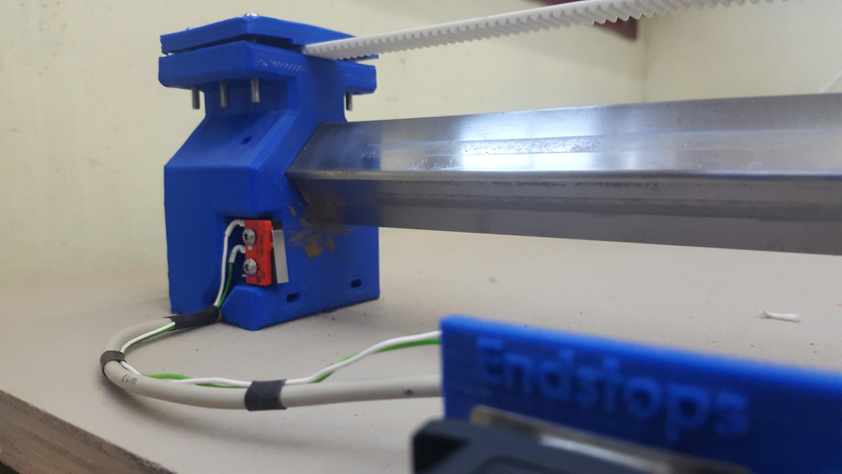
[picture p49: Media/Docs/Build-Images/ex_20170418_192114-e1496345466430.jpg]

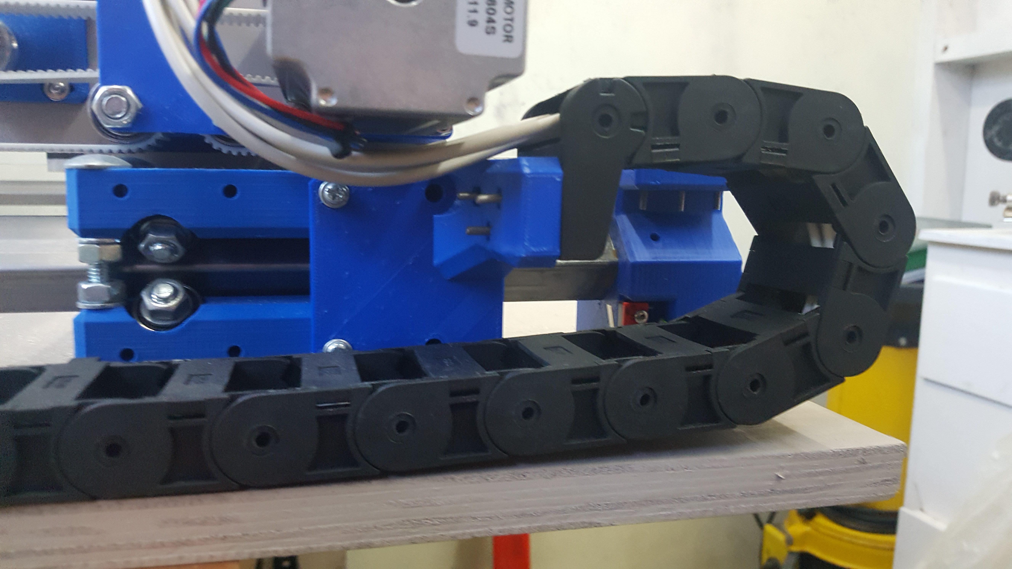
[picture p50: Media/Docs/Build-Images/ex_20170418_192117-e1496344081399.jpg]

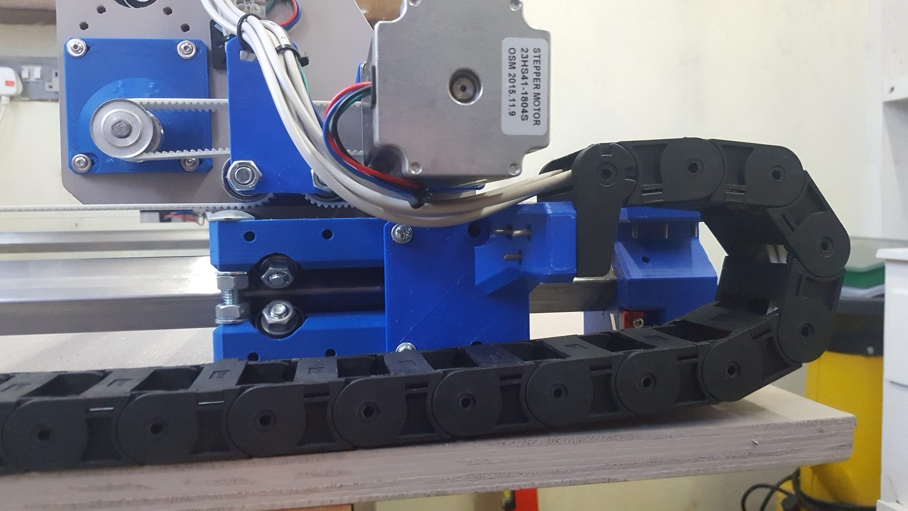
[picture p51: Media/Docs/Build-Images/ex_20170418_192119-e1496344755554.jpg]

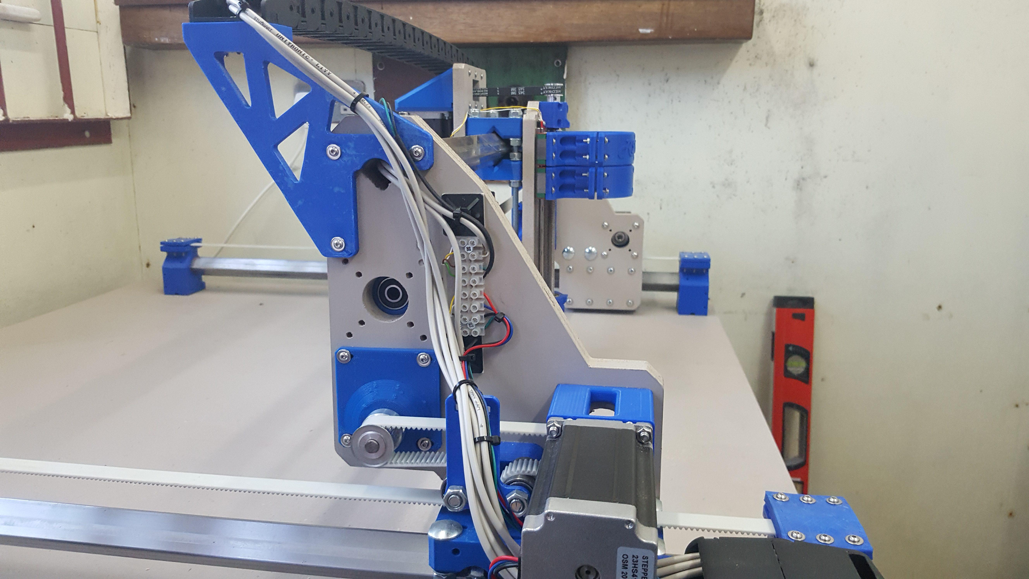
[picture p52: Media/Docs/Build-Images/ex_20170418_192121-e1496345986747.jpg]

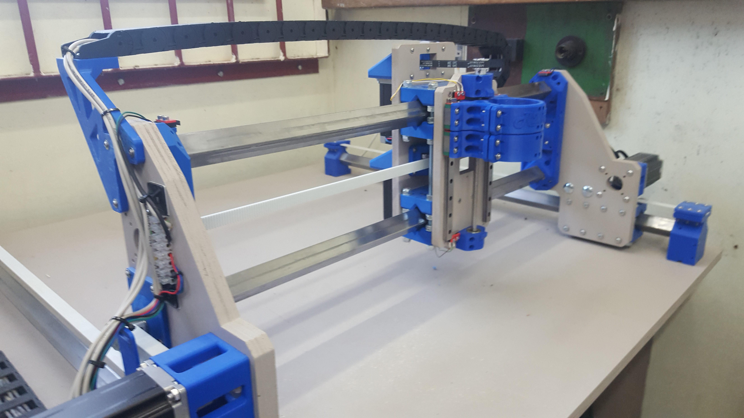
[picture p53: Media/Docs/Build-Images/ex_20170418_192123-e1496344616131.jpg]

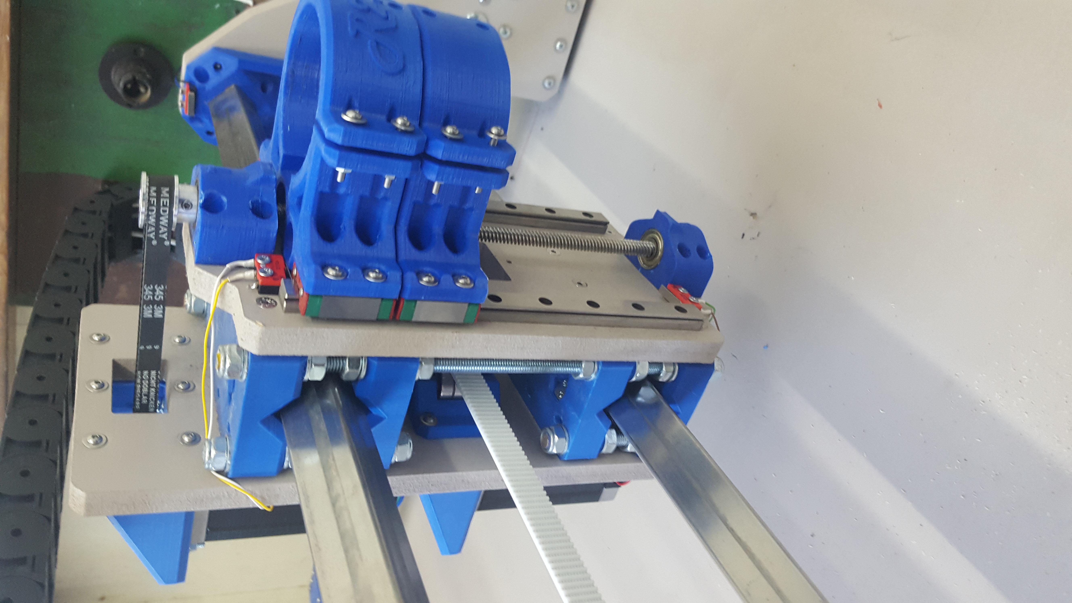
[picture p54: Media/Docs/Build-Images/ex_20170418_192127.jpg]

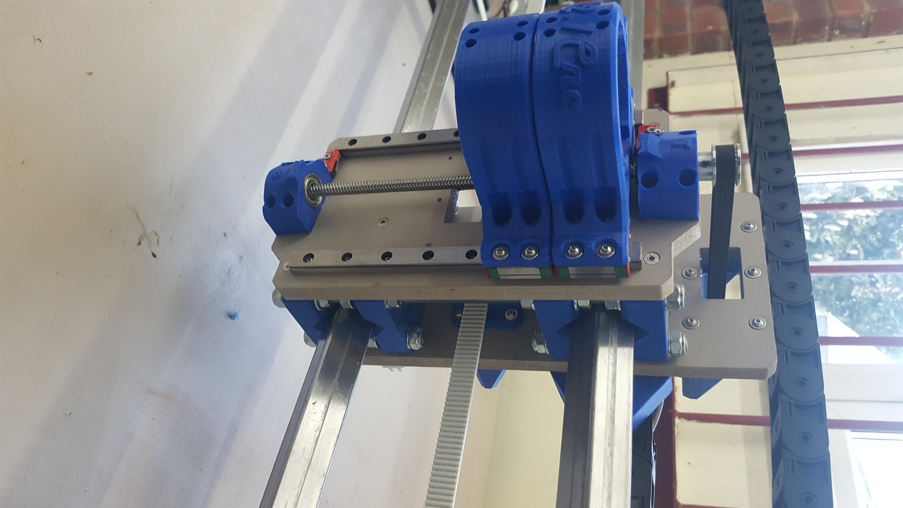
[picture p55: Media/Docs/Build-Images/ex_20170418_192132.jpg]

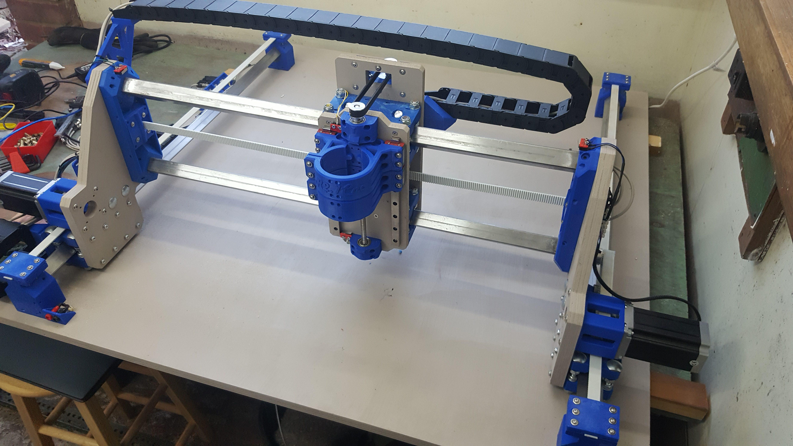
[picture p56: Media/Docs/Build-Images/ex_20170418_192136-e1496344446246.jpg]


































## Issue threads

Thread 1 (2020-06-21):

BOM more details?

ufxela, 2020-06-21:
- What width should timing belt be?
- number of each type of nut/screw which you used? Though this may be tedious to count up...
- bom uses 2.1 instead of 3 in the electronics section
- Maybe amazon/aliexpress/banggood affiliate links? You can make money from these and I'd be more than happy to support you by purchasing from them :)

RootCNC, 2020-06-21:
@ufxela

> What width should timing belt be?

15mm worked well for me - although Root 2 did use 6mm. I'll recommend using the widest you can get both belt and pulleys for.

> number of each type of nut/screw which you used? Though this may be tedious to count up...

extremely tedious, I did count it but kept getting different answers. I typically buy packs of 50 or 100 as they give a better value. but 6, 10, 16, 20, 25, 30, 35mm are a good start for M3 screws. (I'll look to improve this information)

> BOM uses 2.1 instead of 3 in the electronics section

This needs correcting - R2.1 was the release name for Root 3

> Maybe amazon/aliexpress/banggood affiliate links? You can make money from these and I'd be more than happy to support you by purchasing from them :)

Defiantly in the works for Root 4 :) (I'm trying to work out Aliexpress's system for affiliate links) I'll look to improve this for all the machines.

hope that help Pete

Closed 2021-01-24.

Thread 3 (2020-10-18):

Y-Axis Part failure on Belt Clamp

RootCNC, 2020-10-18:
Parts have been failing when tensioning the belt, examples can be found
[Here](https://scontent-lht6-1.xx.fbcdn.net/v/t1.0-0/s261x260/122005073_10158627305983798_998202985164713006_n.jpg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)

RootCNC, 2020-10-18:
Fillets have been added to the affected parts  - please see commit: fabc46801e8ea16fc95369204534f9e9533b3635

NB updated file names will have:

> IssB

 as a suffix.

Closed 2020-10-18.

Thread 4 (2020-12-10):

Marlin 2.0

glyve, 2020-12-10:
Does anyone have a working build of Marlin 2 on the Root 3. I've been trying o get motion right for at least a week and still have random slow moves and freezes during curved or arced moves. Even with toolpath generated without Arcs, is still slows or moves irregularly. Using an MKS SGEN-L Board and Marlin 2.0.6.1

RootCNC, 2021-02-15:
Did you get this solved?

glyve, 2021-02-15:
Thank you for the response.

I didn't get this solved. I moved to a cnc shield using grbl instead and that improved motion but not not at speeds over 1000mm/s. To get that right, I had to use smoothing when generating a 2d contouring toolpath in fusion360.

More info on the marlin problem though, it seemed to stutter most when moving all 3 axes at the same time. So, x and y moving along a curve and z ramping at the same time.

tpeyron, 2021-04-27:
I've just had my Root 3 moving, and I'm using RAMPS1.4 with Marlin 2.0.

I know, it's not yet milling something, but do you guys want me to keep you posted, or should we just shut this topic ?

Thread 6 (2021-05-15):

M5 bolt for motor mount is too short

RootCNC, 2021-05-15:
More information here :https://rootcnc.discourse.group/t/just-starting-down-the-build-road/72/8

proposed change to 80mm length

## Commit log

2020-06-19 First Commit
    First Commit to GitHub
    [Box Section Linear Guild COACH BOLT.STL, Box Section Linear Guild STD.STL, Connector Panel.STL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]
2020-10-18 Added Fillet to reduce the chances of part failure
    [Y Axis Bar Mount 1'x1' 2mm Mirror IssB.STL, Y Axis Bar Mount 1'x1' 2mm Mirror.STL, Y Axis Bar Mount 1'x1' 2mm STD IssB.STL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]
2021-05-06 update to readme and BOM
2021-05-14 Update BOM\README.md
    Minor spellcheck on BOM\README.md
2021-07-08 Adding modified 'Z Axis Bearing Cup Top' to give clearance for router and stop it hitting the upper Z limit tab
    [R3 BOM.xlsx, Z Axis Bearing Cup Top - Limit Tab Removed.stl]
2023-08-12 Added Print
2023-08-12 Added Action and print
2023-08-12 Updated Docs
    [R3 BOM.xlsx]
